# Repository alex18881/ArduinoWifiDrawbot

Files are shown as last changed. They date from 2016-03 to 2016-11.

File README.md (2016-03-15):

# ArduinoWifiDrawbot
Arduino drawing bot with communication over Wifi.

First of all the main idea of this bot is not mine. There are tons of projects in the Internet that inspired and leaded me. Some of them were partially used as base of the project. They are awesome but there are some things should be improved:
1. The bot should get all the data to draw from PC wirelessly
2. The data should be easily edited and transferred
3. The format of data should be standard somehow

Thus the bot should receive data in short version of [G-CODE](http://reprap.org/wiki/G-code). The source image can be created as SVG in the [Incscape](https://inkscape.org/en/) and exported as a g-code file with Incscape plugin [G-Code Tools](https://github.com/cnc-club/gcodetools).

##Overview
The project consists of 3 parts:
1. Printable parts. Parts that can be printed with 3d printer.
2. Arduino firmware.
3. A PC communication software.

Great instructions how to assemble and how to wire the bot can be found here:

http://www.instructables.com/id/Low-Cost-Arduino-Compatible-Drawing-Robot/

##Printable parts
All the chassis parts can be printed on home 3d printer. 

Here's the list of these parts:
1. The chassis: http://www.thingiverse.com/thing:1289315
2. Stepper Brackets: http://www.thingiverse.com/thing:1053267
3. Pen Collar, servo holder and pen holder: http://www.thingiverse.com/thing:1052725
4. Wheels: http://www.thingiverse.com/thing:862438
5. Arduino UNO adapter for the chassis: http://www.thingiverse.com/thing:1397069

Also here you can find a really useful instructions how to calibrate your 3d printer: http://www.thingiverse.com/thing:342198

##Electronics and motors:
1. Arduino UNO (I use one from DX: [Link on DX](http://www.dx.com/p/uno-r3-development-board-microcontroller-mega328p-atmega16u2-compat-for-arduino-blue-black-215600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 and I find it great) )
2. Proto shield (like this one [Link on Ali](http://ru.aliexpress.com/item/ProtoShield-prototype-expansion-board-with-mini-bread-board-based-for-ARDUINO/1451569883.html) )
3. 1 TowerPro SG90 servo
4. 2 28BYj-48 steppers
5. Ball caster with 15mm ball (like this one: [Link on Ali](http://ru.aliexpress.com/item/1pc-Swivel-Round-Ball-Caster-Silver-Metal-Bull-Wheel-Universal-Transfer-Ball-48-x-32-x/32566687062.html) )
6. 1 ULN2803APG stepper driver ( like this one: [Link on Ali](http://ru.aliexpress.com/item/10pcs-ULN2803A-ULN2803APG-ULN2803-DIP-18/32375468380.html) )
7. 1 ESP8266 Esp-01 Wifi module
8. AMS1117 ([Datasheet](http://www.advanced-monolithic.com/pdf/ds1117.pdf))
8. Several 10K resistors for TX and RX Wifi voltage lowering
9. 2 22uF Tantalium and 2 100nF/Ceramic capacitors

##Wiring
Most of the wiring is described in instructions the link on which is in the overview section but there is a mine one placed in the __info__ directory of this project. It includes wifi module.

##Firmware
First: I'm not a professional C++ or Arduino programmer and actually this is my first Arduino project and my C++ experience is limited to about 2 weeks of making small tools 15 years ago for my very first computer. So any help is welcome.

####Used libs:
1. SoftwareSerial (included in Arduino IDE)
2. Servo (included in Arduino IDE)
2. [AccelStepper](http://www.airspayce.com/mikem/arduino/AccelStepper/index.html)

For now I decided to no to use any WIFI library. Previously I used a ITEADLIB_Arduino_WeeESP8266 but then I found useful to have a callback function when a TCP client connects to the bot.

####Supported g-codes:
* G0 - move X### Y###
* G1 X### Y###
* G2 - Arc clockwise
* G3 - Arc counter clockwise
* G4 P### - pause, in milliseconds, G4 S### - pause, in seconds
* G10 - As pen deactivation code
* G11 - As pen activation code
* G28 - move to (0,0)

M-codes:

* M3 - As pen activation code
* M5 - As pen deactivation code

####Wifi
I decided to not to update or reflash the ESP-01 AT firmware even though there are a lot of posts on forums about how bad is its stock firmware. The only thing I did is changing its baud rate to 9600 as it had 115200 and as I read on some forums SoftwareSerial is not really good with big speeds. The command I used for this is: 
`AT+CIOBAUD=9600`
All other commands you can find in [AT Commands document](info/at-commands.md) in info folder.

##Client PC tool
[TBD]

##Thanks to
* Guys from Thingiverse community for their designs. [MakersBox](http://www.thingiverse.com/MakersBox/about) and [FavioR](http://www.thingiverse.com/FavioR/about)

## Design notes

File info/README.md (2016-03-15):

#Info
Here is located some additional and usefull info: Schemes, AT commands, PCB etc.

##Wiring scheme
The wiring scheme contains a voltage regulator. Be carefull the one is used in this scheme is just ASM1117 3.3 with no letters at the end, but there's also ASM1117-REF which requires an ajustable resistor between its ground connector and the ground itself.

The scheme is took from [here](http://arduino.ru/forum/apparatnye-voprosy/podklyuchenie-regulyatora-napryazheniya-ams1117-33v. 
There's also a separate PCB for it in the same post on that page.
Or (here)[https://www.reddit.com/r/esp8266/comments/3f7q0j/best_capacitor_configuration_for_the_esp8266_from/]:
Wifi power

I used the [Fritzing](http://fritzing.org/home/) for the scheme and PCB desings. Here are links on parts for it:

* [AMS1117 regulator](https://github.com/tardate/LittleArduinoProjects/tree/master/FritzingParts/AMS1117)
* [ULN2803 stepper driver](https://github.com/adafruit/Fritzing-Library/blob/master/parts/ULN2803%20Darlington%20Array.fzpz)
* [28byj-48 stepper](https://github.com/tardate/X113647Stepper/blob/master/fritzing_parts/28BYJ-48%20Stepper%20Motor.fzpz)

##AT Commands
[Here](./at-commands.md)

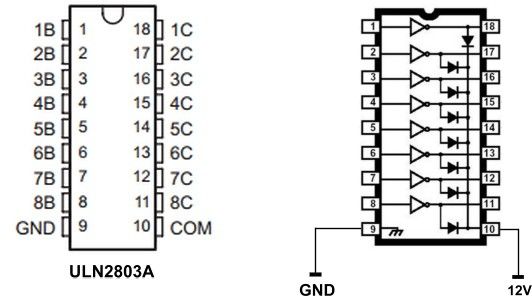
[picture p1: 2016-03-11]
info/F5GB6P0IFOBK3FD.MEDIUM.jpg

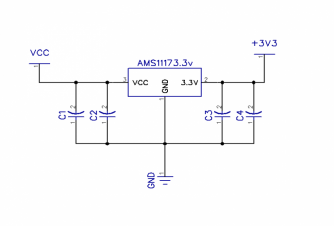
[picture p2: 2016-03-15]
info/asm1117-3.3v-scheme.png

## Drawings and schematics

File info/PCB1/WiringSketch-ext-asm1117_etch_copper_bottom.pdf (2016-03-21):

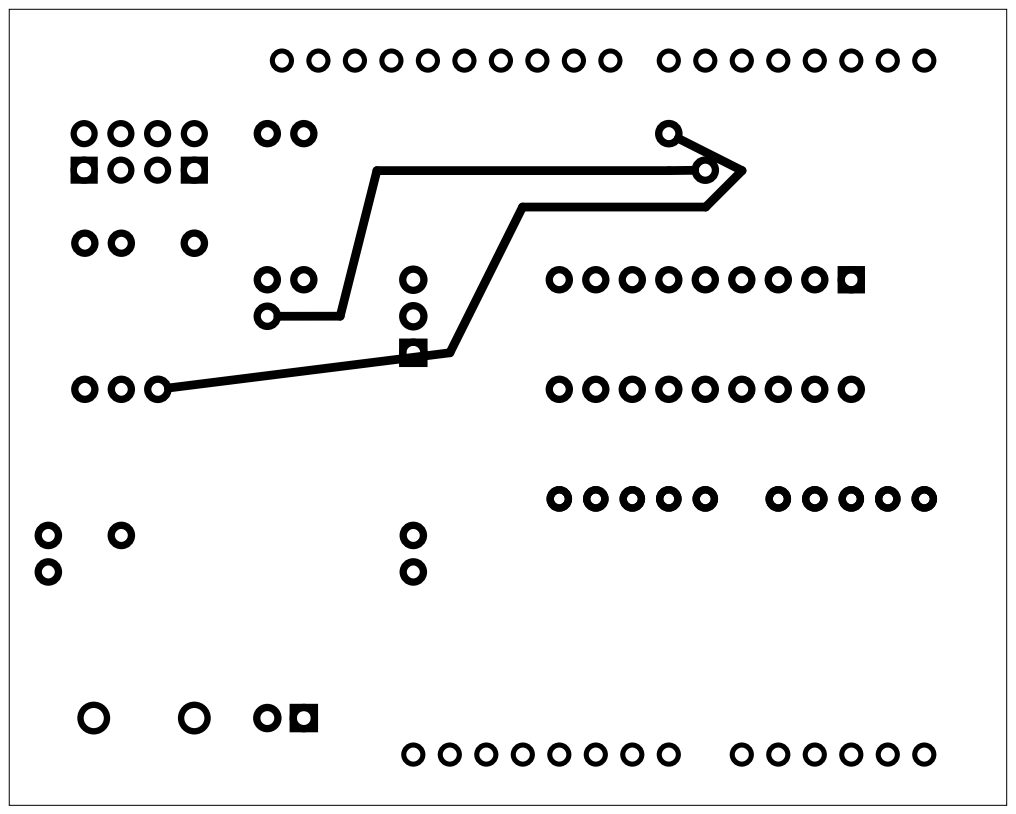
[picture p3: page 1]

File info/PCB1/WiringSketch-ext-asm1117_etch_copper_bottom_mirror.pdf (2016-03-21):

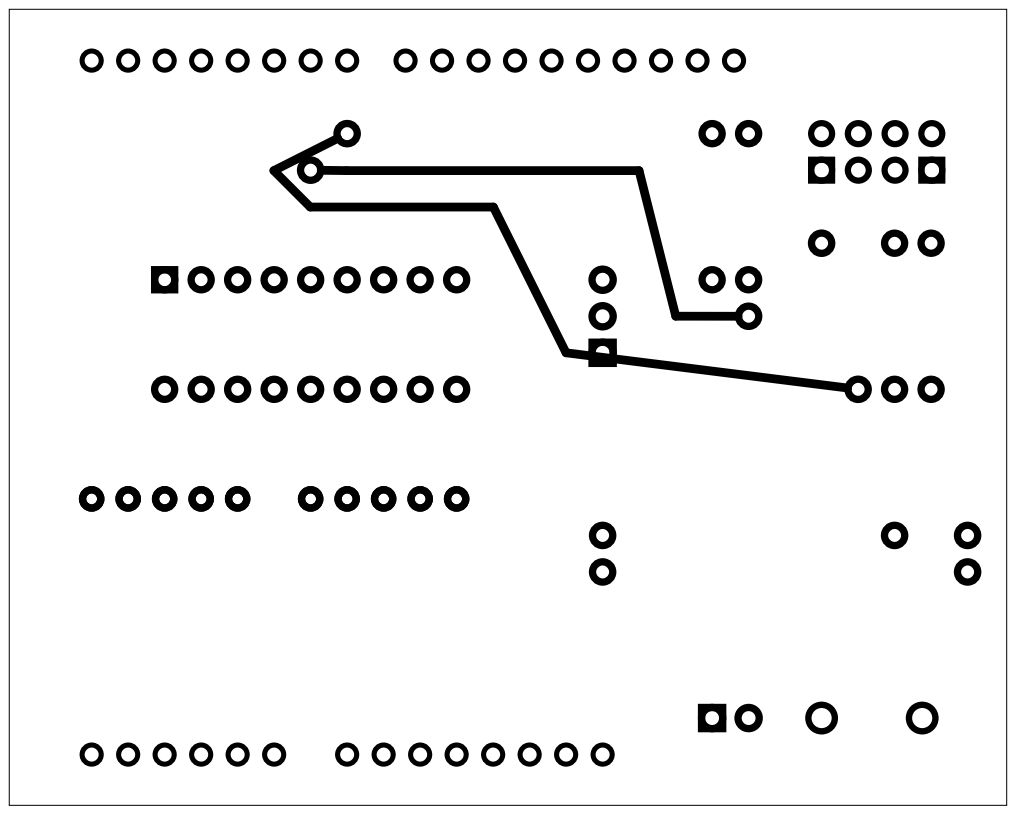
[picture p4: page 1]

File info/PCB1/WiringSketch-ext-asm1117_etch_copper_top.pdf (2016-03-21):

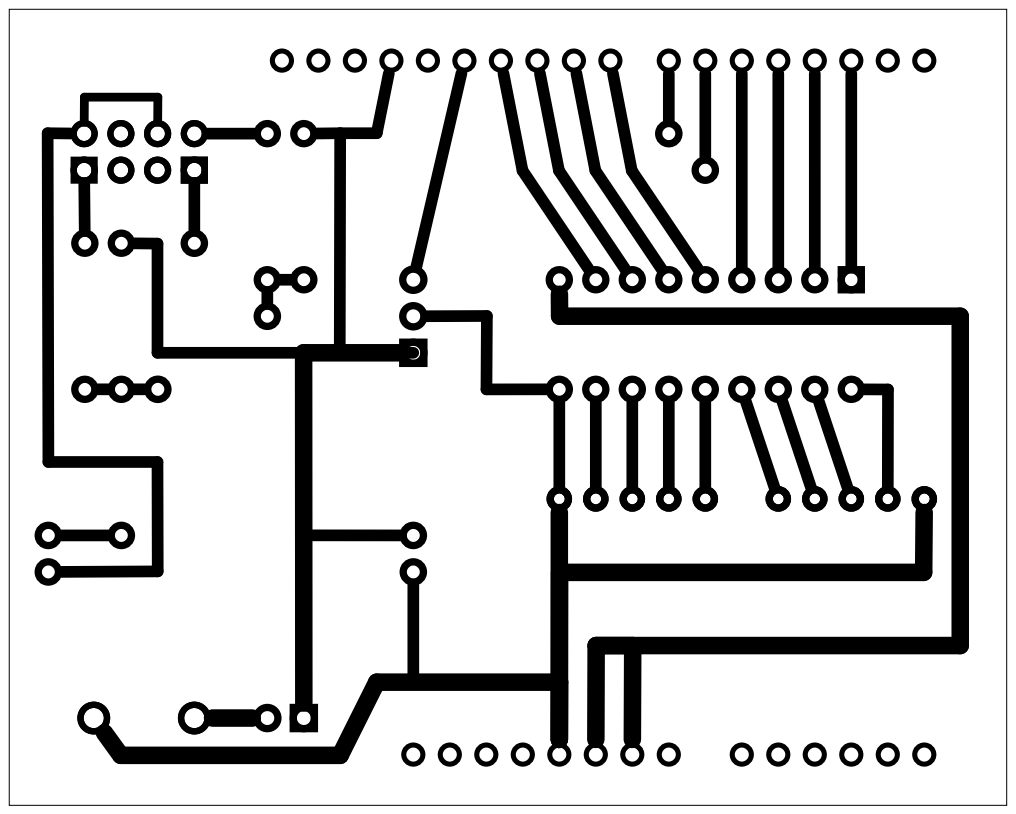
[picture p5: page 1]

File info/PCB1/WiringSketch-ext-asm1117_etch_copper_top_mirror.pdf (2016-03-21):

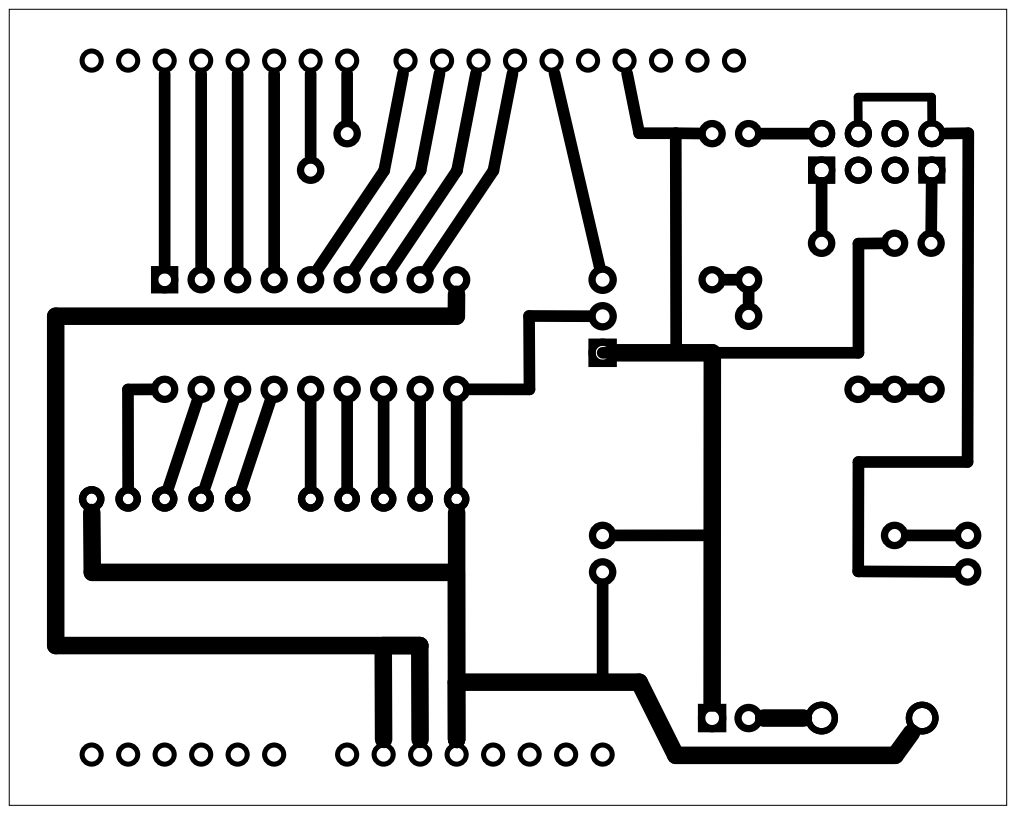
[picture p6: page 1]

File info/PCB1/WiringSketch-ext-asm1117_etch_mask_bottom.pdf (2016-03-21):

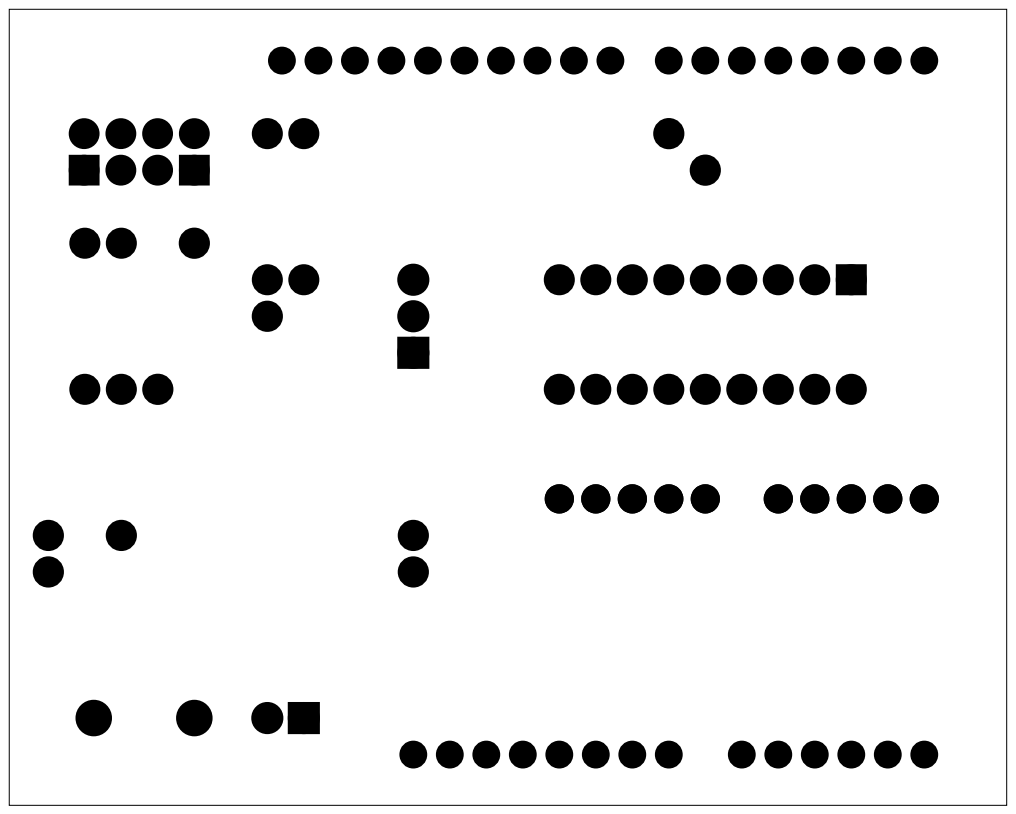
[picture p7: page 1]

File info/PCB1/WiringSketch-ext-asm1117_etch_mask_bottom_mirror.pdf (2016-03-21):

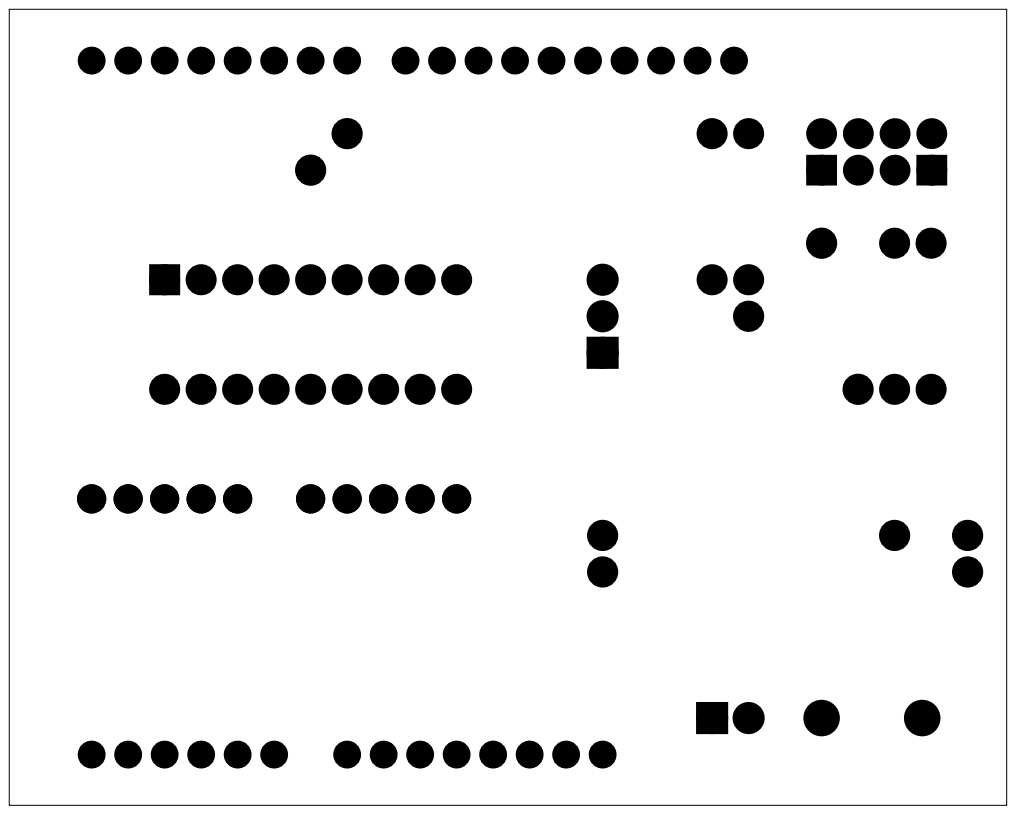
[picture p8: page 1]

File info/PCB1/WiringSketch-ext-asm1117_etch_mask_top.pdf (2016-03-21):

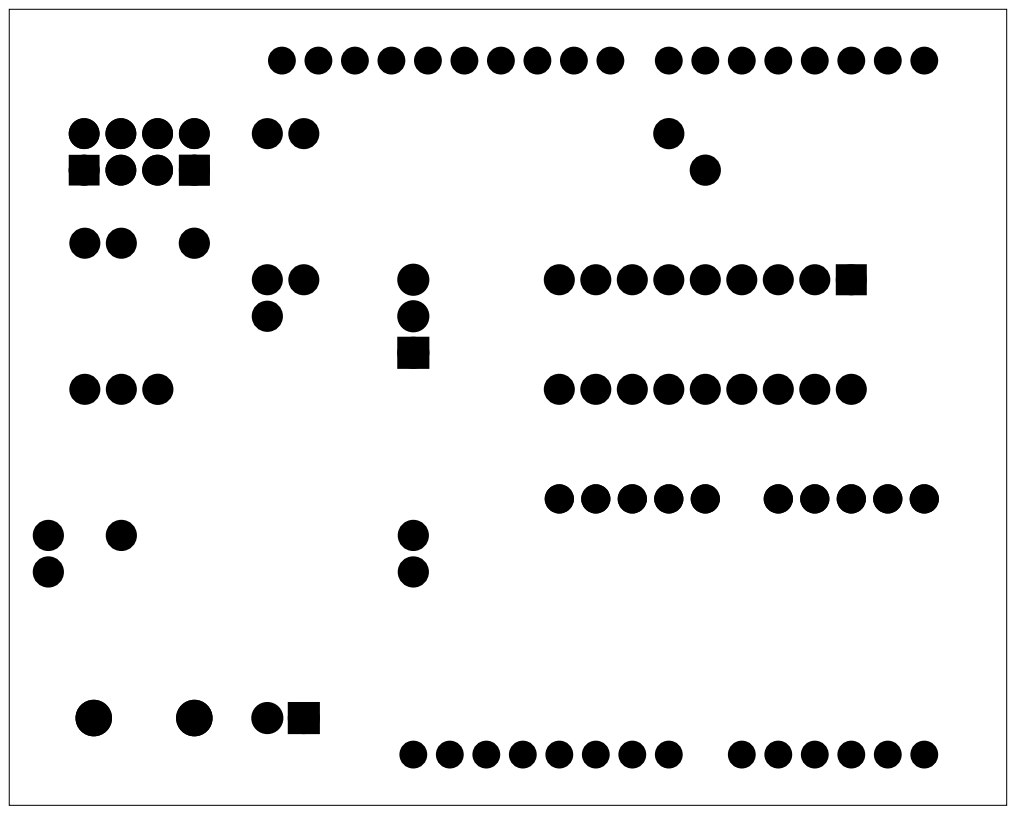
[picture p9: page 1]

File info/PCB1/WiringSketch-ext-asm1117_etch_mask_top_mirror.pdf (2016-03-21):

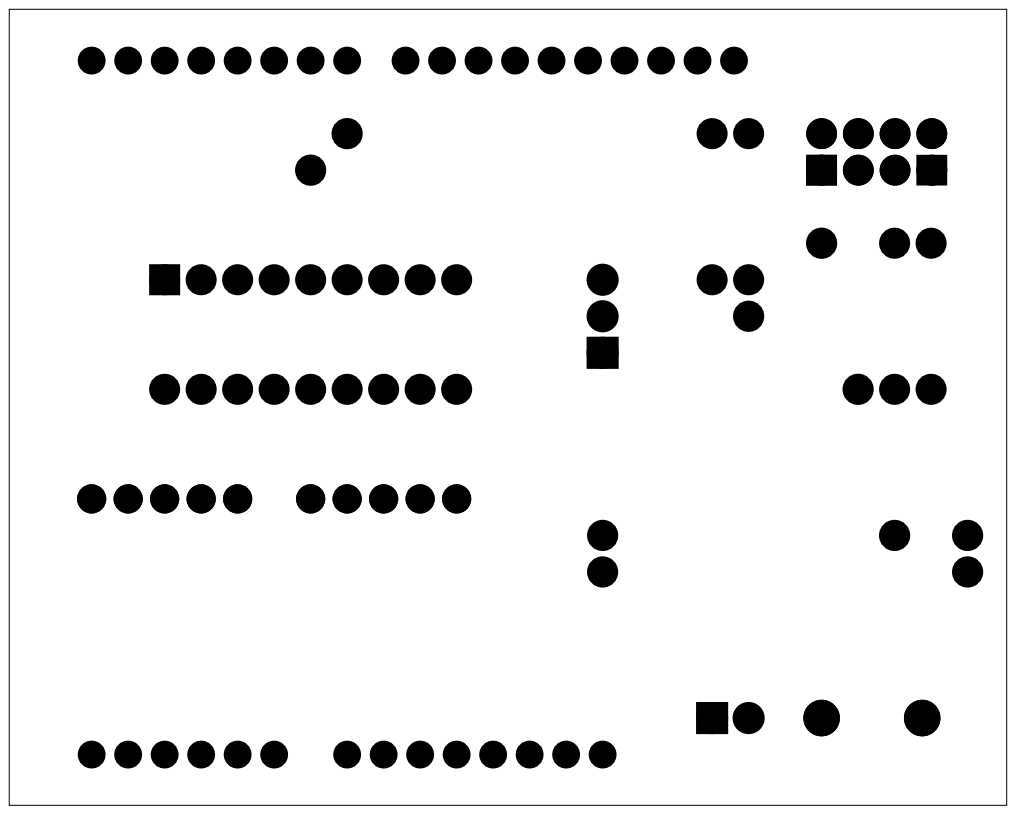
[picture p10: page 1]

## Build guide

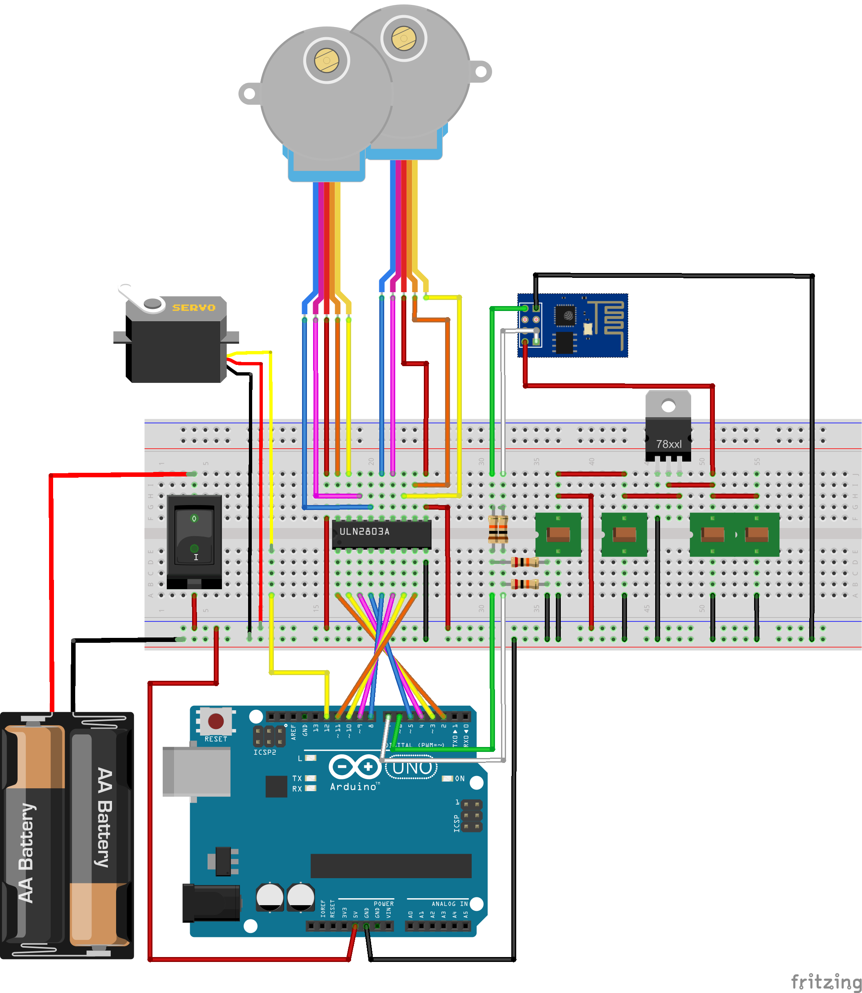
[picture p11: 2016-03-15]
info/wiring.png

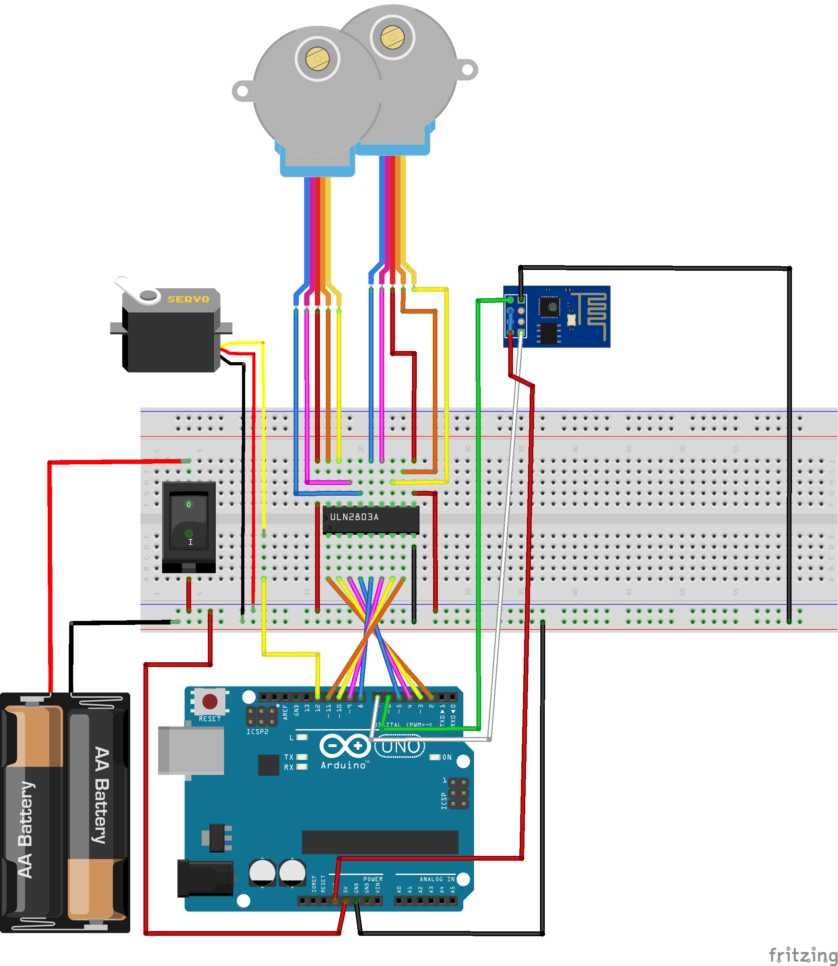
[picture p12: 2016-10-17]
info/WiringSketch-direct3.3_bb.png

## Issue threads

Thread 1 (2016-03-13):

it draws rounded corners sample completely wrong

alex18881, 2016-03-13:
fix M2 and M3 commands

Closed 2016-11-12.

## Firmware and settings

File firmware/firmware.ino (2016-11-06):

#include "Configuration.h";
#include "ConfigManager.h";
#include "drawer.h";

#define FW_VERSION "PROTOCOL_VERSION:" VERSION " FIRMWARE_NAME:" FW_CODE_NAME " MACHINE_TYPE:" MACHINE_NAME

#if defined(WIFI)
#include "wifi.h";
#endif

char buffer[DATA_BUF_SIZE];
bool commandReady = false;
int currBufLen = 0; // how much is in the buffer
int yeldIndx = 0;

char commandG = 'G';
char commandM = 'M';

char paramX = 'X';
char paramY = 'Y';
char paramJ = 'J';
char paramI = 'I';
char paramF = 'F';
char paramS = 'S';
char paramP = 'P';

ConfigManager cfgManager;
Drawer drawer;

#if defined(WIFI)
Wifi wifi;
#endif

void setup() {
	Serial.begin(DATASPEED);
	while (!Serial) {
    	; // wait for serial port to connect. Needed for native USB port only
	}
	cfgManager.read();

	#if defined(WIFI)
	wifi.init(notifyReady, cfgManager);
	#endif
	drawer.init(logMessage, cfgManager);

	drawer.togglePen(false);
  #if !defined(WIFI)
	notifyReady();
  #endif
}

void loop() {
	readSerial();
  
	if( drawer.comandComplete ){
		if( commandReady ){
    		processCommand();
    		notifyReady();
		}
	}
}

#if defined(WIFI)
void readSerial(){
	buffer[0] = (char)0;
	uint32_t len = wifi.read(buffer);
	if( len > 0 ){
    	Serial.print( F("From WIFI[") );
    	Serial.print( len );
    	Serial.print( F( "]: " ) );
    	Serial.print( (String)buffer );
    	Serial.println( (int)buffer[len-1] );

		commandReady = (buffer[0] == commandG || buffer[0] == commandM);// && buffer[len-1] == '\n';
		if(!commandReady)
			notifyReady();
  	}

}
#else
void readSerial(){
	//  Serial.print( "Reading SERIAL" );
	commandReady = false;
	while( !commandReady && Serial.available() ) {
		char c = Serial.read();
		if(currBufLen < DATA_BUF_SIZE){
			Serial.print( c );
			buffer[currBufLen++]=c;
		}

		if(c==';')
			commandReady = true;
	}
}
#endif

void notifyReady(){
	currBufLen = 0;
 	logMessage("\n\n>");
}

void logMessage(String msg) {
	Serial.println( msg );
 #if defined(WIFI)
	wifi.write( msg + '\n' );
 #else
	Serial.print( msg );
 #endif
}

void processCommand() {
	// look for commands that start with 'G'
	yeldIndx = 0;
	int cmd;
	
	float _x;
	float _y;
	float _f;
	float _dx;
	float _dy;

	if( hasValue(commandG) ){
		cmd = parsenumber(commandG);
		
		Serial.print(F("processCommand: command "));
		Serial.println( (String)buffer );

		switch(cmd) {
			//G0 Rapid linear Move
			case 0:
				if( hasValue(paramX) && hasValue(paramY) ){
					_x = parsenumber(paramX);
					_y = parsenumber(paramY);
					_f = parsenumber(paramF);
					drawer.moveTo( _x, _y, _f );
				}
				break;
			//G1 Linear Move: G1 X### Y### F###
			case 1:
				if( hasValue(paramX) && hasValue(paramY) ){
					_x = parsenumber(paramX);
					_y = parsenumber(paramY);
					_f = parsenumber(paramF);
					drawer.moveTo( _x, _y, _f );
				}
				break;
			//G2: Controlled Arc Move Clockwise 
			case 2:
				if( hasValue(paramX) && hasValue(paramY) && hasValue(paramI) && hasValue(paramJ) ){
					_x = parsenumber(paramX);
					_y = parsenumber(paramY);
					_dx = parsenumber(paramI);
					_dy = parsenumber(paramJ);
					_f = parsenumber(paramF);
					drawer.curveTo( _x, _y, _dx, _dy, _f, true );
				}
				break;
			//G3: Controlled Arc Move Counter-Clockwise
			case 3:
				if( hasValue(paramX) && hasValue(paramY) && hasValue(paramI) && hasValue(paramJ) ){
					_x = parsenumber(paramX);
					_y = parsenumber(paramY);
					_f = parsenumber(paramF);
					_dx = parsenumber(paramI);
					_dy = parsenumber(paramJ);
					drawer.curveTo( _x, _y, _dx, _dy, _f, false );
				}
				break;
			//G4: Dwell
			case 4:
				_x = parsenumber(paramP); //in millis
				if( _x == 0 )
					_x = parsenumber(paramS) * 1000; //in seconds
				if( _x > 0 )
					delay(_x);
				break;
			//G10 Retract = remove pen
			case 10:
				drawer.togglePen(false);
				break;
			//G11 Retract = activate pen
			case 11:
				drawer.togglePen(true);
				break;
			//G28: Move to Origin (Home)
			case 28:
				drawer.moveTo( 0, 0, 0 );
				break;
			//G90: Set to Absolute Positioning
			case 90:
				drawer.isRelative = false;
				break;
			//G91: Set to Relative Positioning
			case 91:
				drawer.isRelative = true;
				break;
			//G92: Set Position
			case 92:
				_x = parsenumber(paramX);
				_y = parsenumber(paramY);
				drawer.setPosition(_x, _y);
				break;
			default: break;
		}
	}
	// look for commands that start with 'M'
	yeldIndx = 0;
	if( hasValue(commandM) ){
		cmd = parsenumber(commandM);
		switch(cmd) {
			//M2: Program End
			case 2:
				drawer.rotateTo(0.0, 1.0);
				drawer.reset();
				break;
			//M3: Spindle On, Clockwise = activate pen
			case 3: drawer.togglePen(true); break;
			//M5: Spindle Off = remove pen
			case 5: drawer.togglePen(false); break;
			//M6: Tool change
			//M18: Disable all stepper motors
			//M112: Emergency Stop
			//M114: Get Current Position
			//M115: Get Firmware Version and Capabilities
			case 115:
				logMessage( String(FW_VERSION) );
				break;
			//M201: Set max printing acceleration
			//M500: Store parameters in EEPROM
			case 500: 
				cfgManager.write();
				break;
			//M501: Read parameters from EEPROM
			case 501: 
				cfgManager.read();
				wifi.connect();
				drawer.reset();
				break;
			//M503: Print settings

			default: break;
		}
	}
	commandReady = false;
	yeldIndx = 0;
	// if the string has no G or M commands it will get here and the Arduino will silently ignore it
}

bool hasValue( char search ){
	int i = 0;
	bool result = false;
	while( !result && i < DATA_BUF_SIZE ){
		result = buffer[i++] == search;
	}
	return result;
}

bool isNumPart(char letter) {
	return (isDigit(letter) || letter=='-' || letter == '+' || letter == '.');
}

float parsenumber( char codeType ){
	String val = "";
	bool yeld = true;

	while( buffer[yeldIndx++] != codeType ){
		if(yeldIndx >= DATA_BUF_SIZE ){
			if( !yeld ){
				//Serial.println("Crap command " + (String)codeType + ".");
				yeldIndx = 0;
				return 0.0;
			}else{
				yeld = false;
			}
		}
	}
	//Skipping spaces after command char
	while( !isNumPart(buffer[yeldIndx]) && yeldIndx < DATA_BUF_SIZE ){
		yeldIndx++;
	}

	while( isNumPart(buffer[yeldIndx]) && yeldIndx < DATA_BUF_SIZE ){
		val += (String)buffer[yeldIndx++];
	}

	Serial.print(F("Getting param "));
	Serial.print(codeType);
	Serial.print(F(" = "));
	Serial.println(val);

	if( val == "")
		return 0.0;

	return val.toFloat();
}

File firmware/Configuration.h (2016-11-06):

#define VERSION "0.0.1"
#define FW_CODE_NAME "WallE"
#define MACHINE_NAME "ArduinoWIFIDrawbot"

#define LEFT_WHEEL
#define RIGHT_WHEEL
#define SERVO
#define WIFI

#define DATASPEED             9600
#define DATA_BUF_SIZE         128

#if defined(SERVO)
  #define PEN_SERVO_PIN       12
  #define DRAW_ON_SERVOANGLE  90
  #define DRAW_OFF_SERVOANGLE 0
#endif

#if defined(LEFT_WHEEL) || defined(RIGHT_WHEEL)
  #define WHEELS
  #define HALFSTEP            8 
  #define WHEEL_ENABLE        LOW
  #define WHEEL_DISABLE       HIGH
  
  #define WHEELS_ACCELERATION 10000
  #define WHEELS_SPEED        1000
//  #define WHEELS_MAX_SPEED    1000

// Stepper motors rate: steps per millimeter
  #define WHEEL_STEPS_RATE    20.2931
// 18.8843 - 92.1358
// 20.49616 - 101
// 22.021 - 116.6190

// Base width: the distance between wheels in millimeters.
// Ideally this distance is mesured between centers of weels contact
// patches. Once the pen is located in themiddle of the bot base the
// half of this value is the distance from the actual radiuce to
// radiuces of each wheels paths.
  #define WEEL_BASE_SIZE      113.3
#endif

#if defined(LEFT_WHEEL)
  #define LEFT_WHEEL_PIN1     2
  #define LEFT_WHEEL_PIN2     3
  #define LEFT_WHEEL_PIN3     4
  #define LEFT_WHEEL_PIN4     5
#endif

#if defined(RIGHT_WHEEL)
  #define RIGHT_WHEEL_PIN1     8
  #define RIGHT_WHEEL_PIN2     9
  #define RIGHT_WHEEL_PIN3     10
  #define RIGHT_WHEEL_PIN4     11
#endif

#if defined(WIFI)
  #define WIFI_DATASPEED      9600
  #define WIFI_SSID           "BoogymanHomeWifi"
  #define WIFI_PASSWORD       "alex18881"
  #define WIFI_TX_PIN         7
  #define WIFI_RX_PIN         6
  #define WIFI_SERVER_PORT    1336
  #define WIFI_COMMAND_TIMEOUT 1000
#endif

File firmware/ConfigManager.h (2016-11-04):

#ifndef CFGMNGR_H
	#define CFGMNGR_H

#include <Arduino.h>; //needed for Serial.println
#include <EEPROM.h>;
#include <string.h>;
#include "Configuration.h";

class ConfigManager {
	public:
		ConfigManager();

		void read();
		void write();

		char *SSID = (char *)WIFI_SSID;
		char *passwd = WIFI_PASSWORD;
		int wifiPort = WIFI_SERVER_PORT;
		int wifiBodRate = WIFI_DATASPEED;

		float wheelsAcceleration = WHEELS_ACCELERATION;
		float wheelsSpeed = WHEELS_SPEED;
		float wheelsStepRate = WHEEL_STEPS_RATE;
		float wheelsBaseWidth = WEEL_BASE_SIZE;

		float wheelsBaseHalfWidth;

	private:
		typedef struct _cfg {
			char *ssid;
			char *pwd;
			int port;
			int bodRate;

			float acceleration;
			float speed;
			float stepRate;
			float baseWidth;
		} Config;
};

#endif

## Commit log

2016-03-12 added firmware and nodejs client
    [Configuration.h]
2016-03-13 added test g-codes. Rotation fixed
    [Configuration.h]
2016-03-13 wiring scheme update
2016-03-13 Fixed miroring. Added rounded corners ssquare G-Code sample
    [Configuration.h]
2016-03-15 Added ASM1117 3.3v scheme
2016-03-15 Sheme improvements
    [WiringSketch.fzz]
2016-03-21 2 PCBs + firmware update
    [Configuration.h, WiringSketch-ext-asm1117.fzz]
2016-06-13 new PCB without WIFI power module + M2/M3 fix
    [WiringSketch-direct3.3.fzz]
2016-10-17 Node client is now a web-server
    [WiringSketch-ext-asm1117.fzz]
2016-10-25 Command params fix
    [Configuration.h]
2016-10-27 Speedup. Commands buffer incresed to 128 bytes
    [Configuration.h]
2016-10-29 Added EEPROM support. M500 and M501 codes
    [Configuration.h]
2016-11-04 FW fix
    [Configuration.h]
2016-11-06 M115 g-code support added
    [Configuration.h]
